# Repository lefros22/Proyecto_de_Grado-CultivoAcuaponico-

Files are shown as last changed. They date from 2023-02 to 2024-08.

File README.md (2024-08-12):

# Degree_Project-AquaponicCrop

In this repository you will find the documentation of "Design and implementation of an automation and control system for aquaponic crops in urban areas".

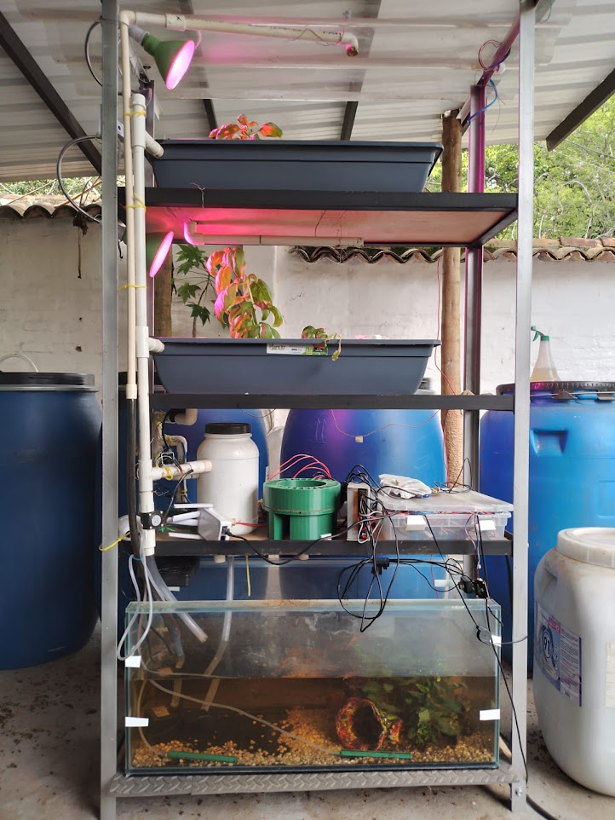
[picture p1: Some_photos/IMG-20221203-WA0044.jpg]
My Image


The main document is written in Spanish, but the documentation in this repository is in English.

Authors: 
- Luis Fernando Riveros Orozco
- Karen Yissel Marin Franco

Director:
- Juan Manuel Nogales

## Project summary
The project is the assembly of an aquaponic crop and the implementation of an automation system using hybrid predictive control with fuzzy to control the active elements of the crop.

The entire project is divided into the following components:
- Physical structure
- Web page
- IoT
- Control
- Management system

### Resume: 

This work presents an automation and control system for aquaponic crops in urban environments by employing a modern multivariable control technique. The prototype reached a level 7 on the Technology Readiness Level (TRL) scale and consists of an aquaponic crop in which water luminosity and temperature are controlled through a hybrid predictive control with fuzzy logic applied to four fundamental control variables: water oxygenation, circulation and aeration, and plant luminosity.

To operate the automation system, a webpage was built to provide access to remote control, supervision, and monitoring functionalities, as well as a management system based on Linux services and communicates via MQTT. The automation system uses a local network that allows communication between different system components (sensors, actuators, microprocessor, and microcontroller) and is capable of detecting internet connectivity status and taking actions in case of failure. Furthermore, the prototype demonstrates complete autonomy for a period of 3-5 days, attributed to the incorporation of a feeding dispenser. Moreover, the prototype also exhibits a semi-autonomous functionality of up to 20 days, achieved by regular replenishment of the dispenser every 4 days and maintenance of the filters by cleaning every 6 days

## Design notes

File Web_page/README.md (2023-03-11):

# Web Page

Technical description of the website:

- Server: hosted in firebase under the backendless paradigm.
- Technology: Node.js with the react framework.
- Database: firebase real-time.
- Architecture: By components, reusable views, OOP.

Here you can see:
- Desing process of the page
- Source code of the page
- Final views of the page

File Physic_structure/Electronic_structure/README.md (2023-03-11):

# Electronic_structure

In this folder you can see:

- ESP32_code: final code used in the proyect
- Dosage: Files of fedders
- Sensors_Detail: The detail of the sensor used in the project

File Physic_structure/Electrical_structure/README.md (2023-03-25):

# Electrical structure
Here you can see the used cable list

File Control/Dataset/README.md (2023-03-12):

# Dataset
Here you can see the excel files with the data used or generated in the notebooks

I consider it important to talk about "estimulos.xlsx" since it contains the combinations of the cycles applied in the data collection stage.

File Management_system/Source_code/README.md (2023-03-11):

# Management system

This folder contains the source code of the management system and the services files

## Folders: 

- **servicios:** the source code of program

- **services systemd:** the configuration archives to sytemd

- **service crontab:** the linux command for services in crontab

## Explanation of each of solution

### services executed with crontab
- Webcam: takes twenty photos, one photo every three seconds, and stores it in ram (Managed by crontab, runs it every minute).
- AskInternet: pings google and if successful, stores in ram(statusInternet) the value 'ON' that represents internet connectivity.

### python services executed with systemd
#### BD reading:
- **EstadoControl_service:** it is a listener of the control state in which the DB is found in the location "Control/stateControl" corresponding to the state of the control (Manual, Automatic, Emergency) and writes it to a ram file located in "Ram_Var/estado.txt”.
- **EstadoActuadores_service:** it is a listener of the actuators state that is found in "Control/Actuators" and when a change occurs, it writes it to a ram file "Ram_Var/actuadores.txt".
#### DB writing:
- **ActPinesBD_service:** subscribes to the "main/actuadores" topic, manages a JSON that contains the status that each actuator must have and when it receives a message, it updates (set) the status that was sent to it in the DB in the "Control/Actuadores" location .
- **SensoresBD_service:** It subscribes to the “esp32/sensor” topic, it manages a JSON that contains the measurement of the esp32 sensors and when it receives a message, it adds (push) the status that was sent to it in BD in the “DatosSensoresInterno” location.
- **MensajesBD_service:** is subscribed to the topic “main/mensajes” and when it receives a message, it sends it (push) to BD in the location “Mensajes”.
- **SensoresExtBD:** is subscribed to the topic “Main/sensorExr/#“ and when it receives a measurement result, it sends it (push) to BD in the location “DatosSensoresExterno”.
- **PredictionsBD_service:** is subscribed to the “PredictionsBD” topic and when it receives a result from the work cycles, it sends (push) them to BD in the “ControlPredictivoResult” location.
#### Publishers in mqtt
- **Desague_service:** reads the status of a GPIO port of the raspberry (drain sensor found in the drainage module of the physical assembly) and publishes an emergency message in the "main/messages" topic if activated.
- **LightSensor_service:** reads the result of an I2C luminosity sensor every minute and publishes the average of the measurement every two hours in the topic “Main/sensorExr/Ligth”.
- **ControlModerno:** it is a service of the execution type with a timer which is executed automatically every two hours and makes the prediction of the best combination of stimuli for the next interval, which writes in Ram ("Ram_Var/ciclos_pred.txt") and sends a message to the topic “PredictionsBD”.

#### Main
- **MainControl:** is the main service that reads variables stored in RAM and publishes to MQTT using commands with the subsystem library. It manages the ignition of the actuators depending on the time of day and also manages the measurement and dosage of feed. This service implements two threads, one for water circulation and the other for sensing. Additionally, depending on the internet connectivity, it activates the ON/OFF control as an emergency system, since the predictive needs information from the internet.
#### Others
- **PinesActuators:** it subscribes to the "main/actuatuadores" topic, it manages a JSON that contains the status that each actuator must have and when it receives a message, it updates the status that was sent to it in the GPIO ports.

### Python scripts:
- **Control_module:** contains two functions
  - *Porcentajes:* returns what status the different actuators should have depending on the time of day according to a predefined Json file.
  - *get_Porcentajes_predictivo:* returns the working percentages for the actuators according to the current state of the predictive control.

- **PictureBD:** Reads an image from the BD every three seconds, converts it to base64, and sends it to the BD.

- **RN:** script that loads the models (ML model, scaler dimensional model, standard scaler) and contains a function that executes the prediction by going through the three models.
- **FUZZY:** script that generates the value that should be applied according to the previous luminosity average.

### Files:
#### Models:
- **RNmodel:** model corresponding to the neural network (sklearn MLPregressor).
- **dim_scaler:** dimensional reduction model (sklearn PCA decomposition).
- **std_scaler:** normalization model (sklearn StandardScaler).

#### Variables in ram:
- **actuadores:** JSON file with the status of each actuator in the database.
- **status:** control status value (manual, automatic, emergency) found in the database.
- **last1Lum_sensor:** The last average luminosity measured.
- **last6_sensor:** JSON file with the record of the last 6 values measured in the fish tank.
- **ciclos_pred:** JSON file corresponding to the work percentages calculated by the predictive control.
- **Captura.jpg:** image corresponding to the photo captured by the camera
- **statusInternet:** value corresponding to the internet status

## ADDITIONAL
### Libraries used in this project

#### For Raspberry:

- **Mosquitto-broker:** used to set the raspberry pi as a bróker mqtt 
  - https://randomnerdtutorials.com/how-to-install-mosquitto-broker-on-raspberry-pi/

- **Mosquitto-client:** used to set the raspberry pi as a client mqtt
  - https://randomnerdtutorials.com/testing-mosquitto-broker-and-client-on-raspbbery-pi/

- **fswebcam:** used to take photos from usb camera in webcam.sh

#### For python:

- **paho.mqtt.client:** used for suscribe and create a client in python script
- **pyrebase:** used for make the conection to bd firebase-realtime
  - https://github.com/thisbejim/Pyrebase
- **DateTime:** used to get the current time and convert between date formats
- **rpi.gpio:** used to control the gpios of the raspberry and control the elements of action.
  - https://www.raspberrypi-spy.co.uk/2012/05/install-rpi-gpio-python-library/
- **smbus2:** used to read the measurement of the brightness sensor BH1750
  - [https://www.pololu.com/docs/0J73/15.9](https://www.pololu.com/docs/0J73/15.9)

### How to mount a space in ram
Replace "full_path" with the exact path where you want the ram folder, not including the "[]", also you can change the size in size, actual size is 30mb in the command
#### `sudo mount -t tmpfs -o rw,size=30m tmpfs [full_path]`

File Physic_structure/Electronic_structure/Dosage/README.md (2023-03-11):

# Dosage
STL files of the 2 versions of the feder together with an assembly 3d diagram

- Feeder Version 1: Feeder by storage hopper and endless screw driven by nema 17.
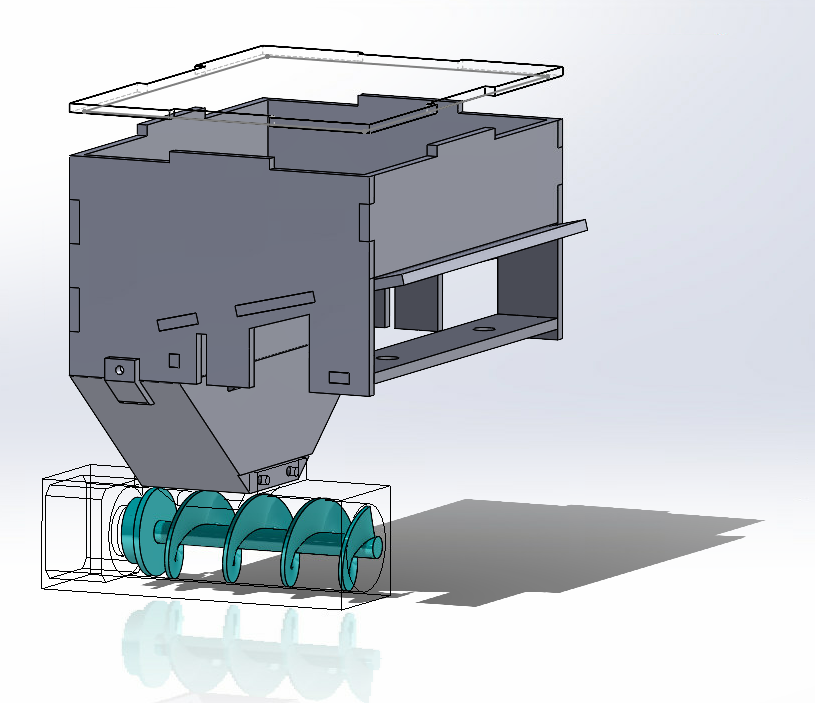
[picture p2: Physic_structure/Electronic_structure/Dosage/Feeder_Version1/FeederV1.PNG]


- Feeder Version 2: volumetric type doser by cell rotation powered by nema 17 and set of pulleys.
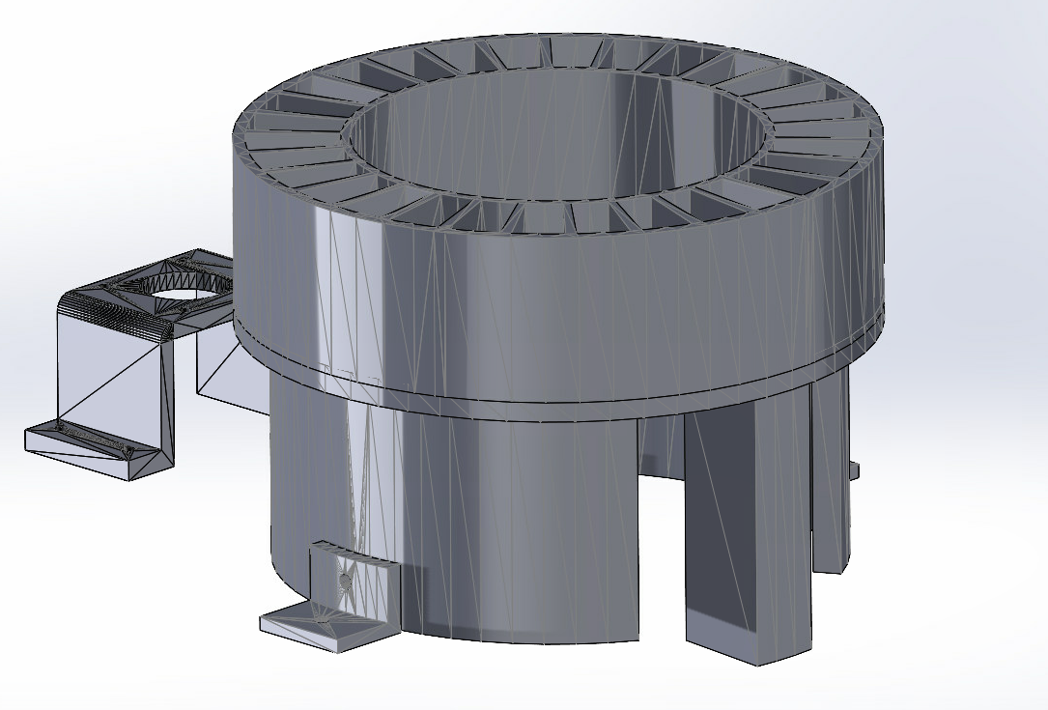
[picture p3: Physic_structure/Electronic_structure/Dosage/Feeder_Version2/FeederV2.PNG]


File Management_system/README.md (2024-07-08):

# Management system
This folder contains the documentation of the management system

The Management System it's implemented under services architecture using systemd and crontab in Linux with scripts in Python and Bash.

- Complete diagram of the architecture of services, modules and components

- Description of each script

- Script codes

- Service codes

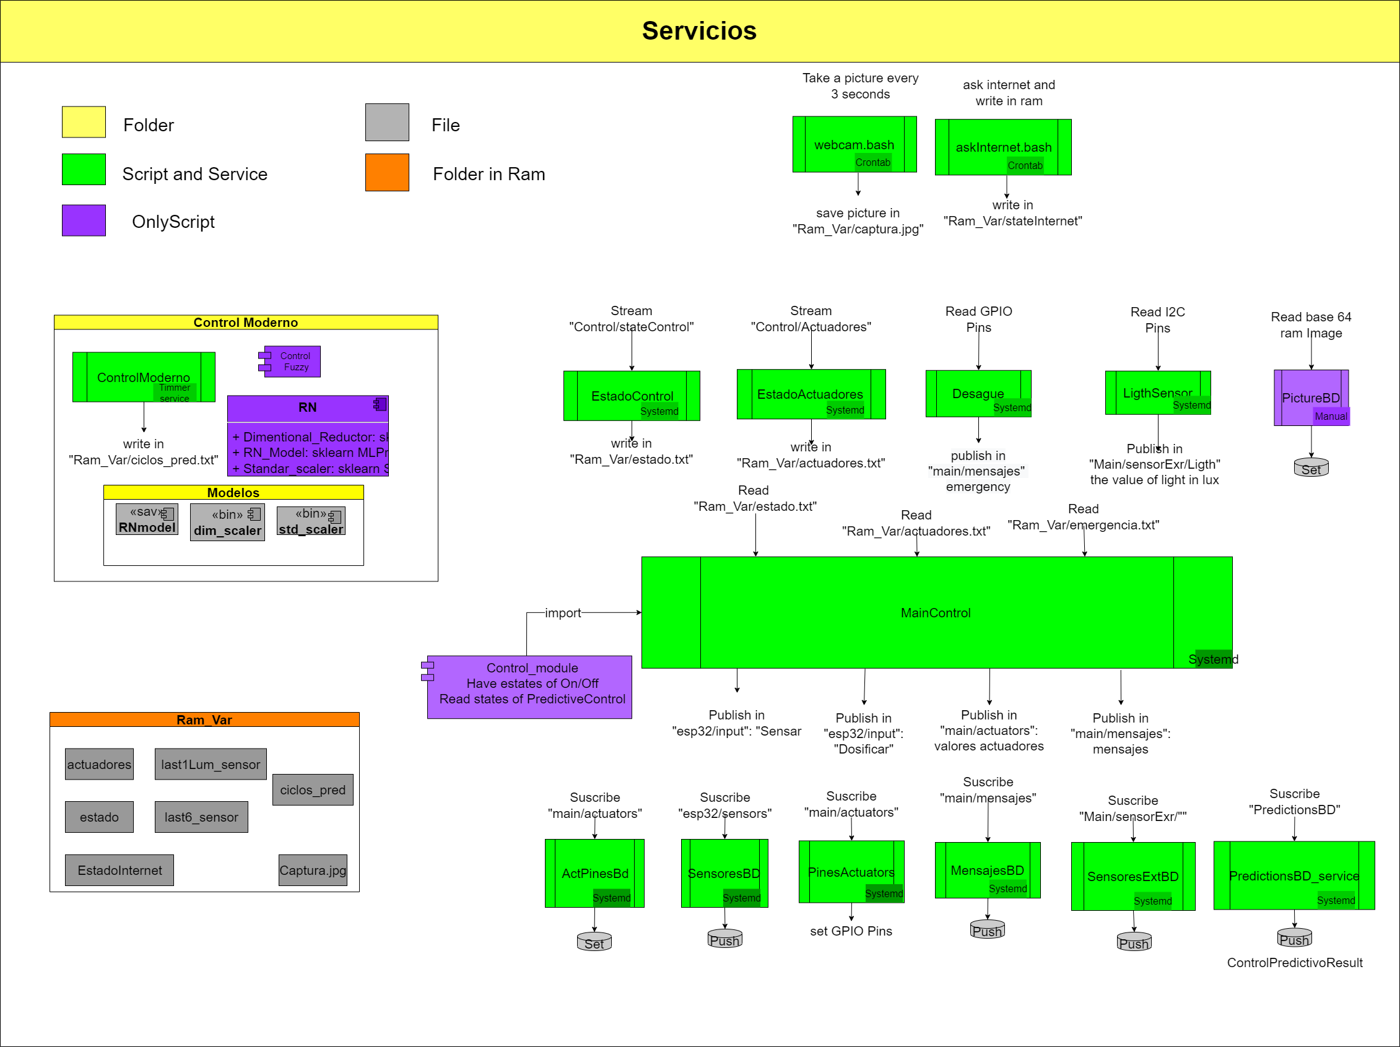
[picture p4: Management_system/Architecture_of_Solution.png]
My Image


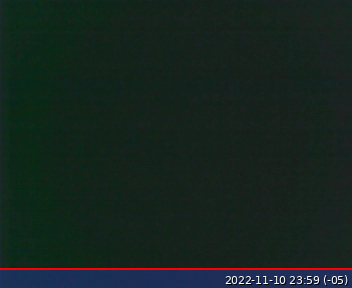
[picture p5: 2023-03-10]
Management_system/Source_code/Servicios/Ram_Var/captura.jpg

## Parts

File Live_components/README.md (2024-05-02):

# Live componets
Live components of the project are:

- Fishes
- Plants
- Bacteria

The photos in the nex link:

https://photos.app.goo.gl/17TKQxqVfbyk1X739

For description you can check the grade project document

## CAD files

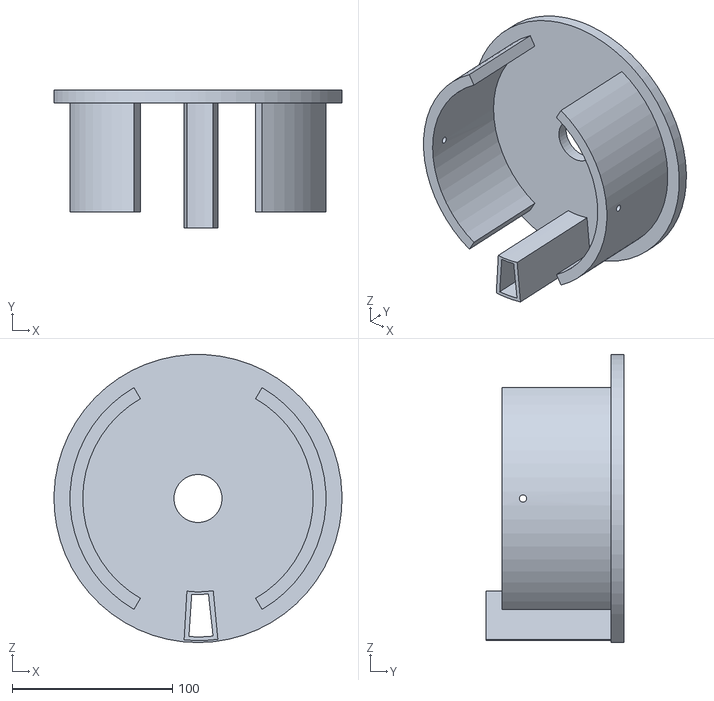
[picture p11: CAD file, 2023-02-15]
Physic_structure/Electronic_structure/Dosage/Feeder_Version2/pieza3.STL
179.9 x 86.0 x 180.0

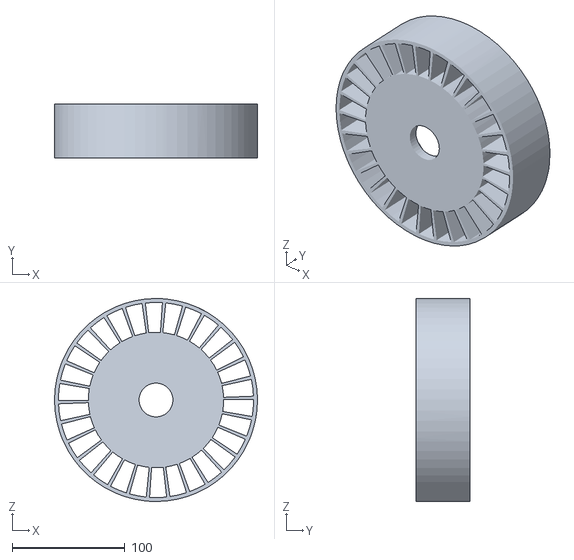
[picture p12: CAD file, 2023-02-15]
Physic_structure/Electronic_structure/Dosage/Feeder_Version2/pieza1.STL
180.0 x 48.0 x 180.0

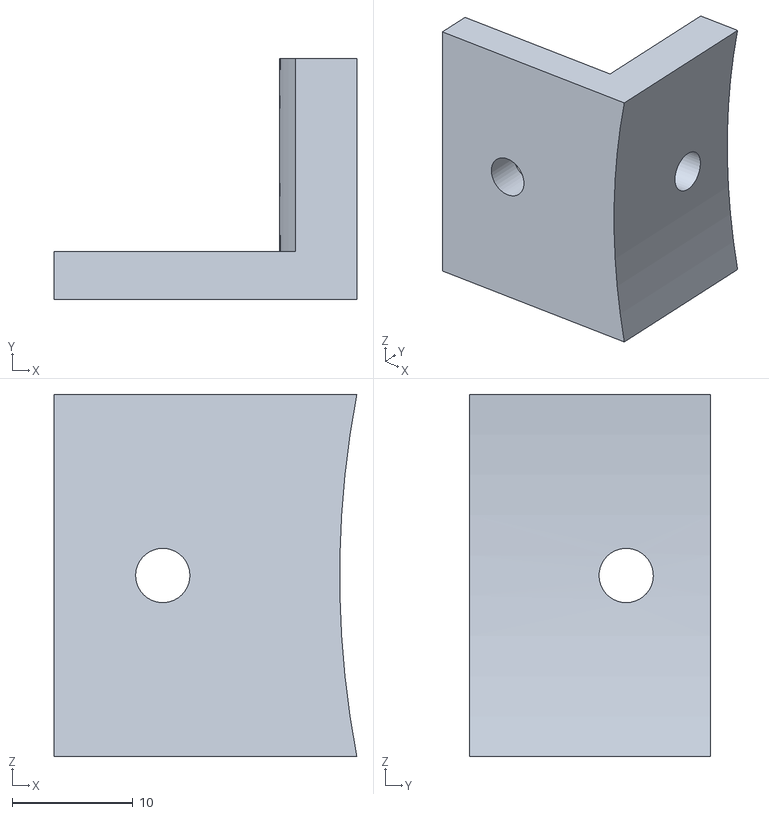
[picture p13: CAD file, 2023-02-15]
Physic_structure/Electronic_structure/Dosage/Feeder_Version2/pieza4x2.STL
25.1 x 20.0 x 30.0

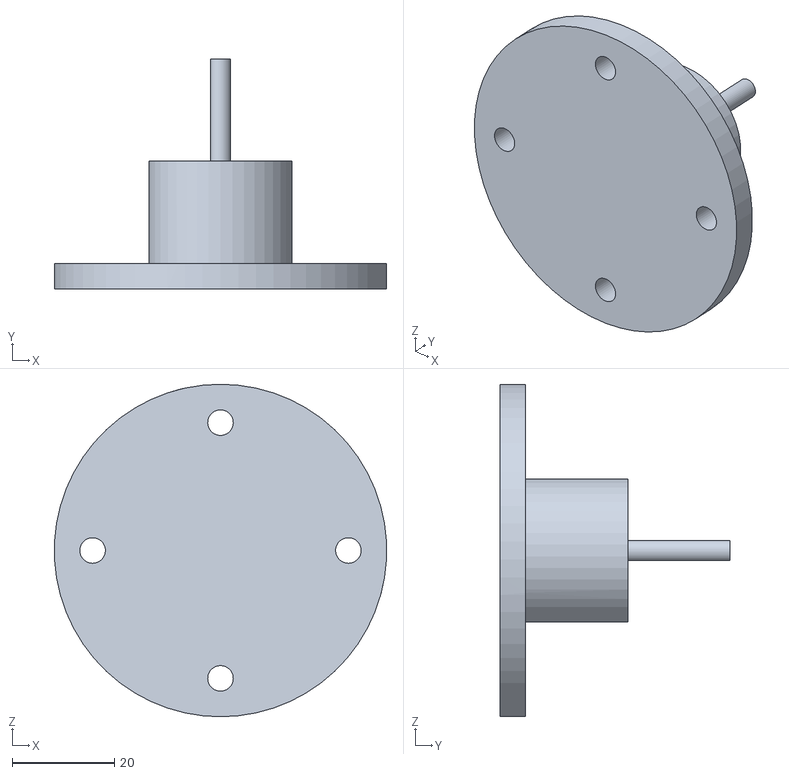
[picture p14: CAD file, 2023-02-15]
Physic_structure/Electronic_structure/Dosage/Feeder_Version2/pieza2.STL
64.9 x 45.0 x 65.0

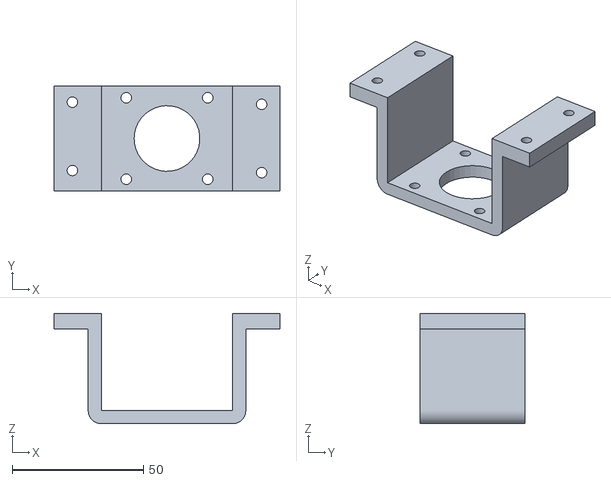
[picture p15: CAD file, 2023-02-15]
Physic_structure/Electronic_structure/Dosage/Feeder_Version2/pieza5.STL
86.0 x 40.0 x 42.0

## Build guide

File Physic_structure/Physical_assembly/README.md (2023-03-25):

# Physic structure

Here you can see the used pipe materials

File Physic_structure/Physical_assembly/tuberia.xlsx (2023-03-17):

Imagen | Nombre | Cantidad
 | Tubo presión 1/2-pulg x 6mts 9-500 PSI | 1
 | Unión hembra roscada 1/2 Presión | 16
 | Codo 90 x 1/2 presión | 24
 | Tee 1/2 presión | 8
 | Unión 1/2 presión | 8
 | Tapon Roscado Presión 1/2 | 2
 | Adaptador Macho Presión 1/2 | 2

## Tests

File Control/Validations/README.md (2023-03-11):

# RN

- **Correlation Matrix Notebook:** Here you can see an example of the notebook used to evaluate the correlation in a time interval, only that it can be subject to bias due to the complexity in the interactions of the system, it is more a reference measure than an accurate validation.
- **Control validation Excel:** To analyze how consistently the network responded based on different data and conditions, 30 random samples were extracted from the dataset and the percentages of cycles were iterated in the 16 possible peak combinations (0%, 100%) in each of the actuators.
The results were consistent for all 30 samples. In this file you can see a summary table with the calculations made for 10 neural networks.

  - In sheet Combination strategy you can find the 16 combinations of maximum and minimum used in the analysis
  - In sheet Analysis you can find the nex tables:
    - ***Comparison with respect to not exercising actions:*** In this table you can see the variation of each of the action sets with respect to set 0 (do nothing, review the previous page).From here, the maximum possible real variation is obtained, which is the subtraction between the maximum positive variation vs. the maximum negative variation, with which the real variation is obtained.
    - ***Mean step response for each variable:*** Here is summarized the variation of the previous table for the unit step responses of each of the action variables while the rest are set to 0. In addition, it is calculated how representative this change is in contrast to the maximum possible variation between cases of the previous table
    - ***Sign consistency in changes:*** Here the consistency of the variations is analyzed, seen in another way, if the variations are an accidental or real fact that the network manages to interpret, the results indicated that for TDS 10/10 networks generate the same sign of variation (positive or negative). in each of the 16 cases, while for Temperature 97% of the cases are consistent.

## Conclusion
According to the previous results, it is validated that the system is controllable to some extent indirectly.

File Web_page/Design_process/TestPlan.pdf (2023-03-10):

Propuesta de plan de pruebas

Teniendo en cuenta la etapa en la que se encuentra el proyecto. Aún no se puede comprobar la funcionalidad en la vida real (pues aún no está montado el cultivo) y además las interacciones con el usuario no están implementadas por completo.

Lo que sí podemos evaluar, son las funcionalidades principales que ya se encuentran dentro de la aplicación web y la dinámica de usuario al momento de usar la app.

Se decidió hacer una entrevista vía zoom en donde el usuario en un primer momento se le da una contextualización del proyecto, posteriormente se le deja controlar la pantalla para usar la app web y por último se le da una encuesta al final de la sesión.

La encuesta se divide en 4 partes:

-Interfaz: en la cual se evalúan los colores y la tipografía.

-Funcionalidades de monitoreo: en la cual se pregunta si las funcionalidades que posee la página son claras, pues las interacciones no están completamente implementadas y la parte gráfica tampoco está hecha por completo.

-Funcionalidades de control: una sección en donde se evalúa estándar y claridad para un usuario conocedor del tema(pues no está pensado para cualquier persona) sin embargo si se deja espacio de opiniones para otro tipo de usuario(que solo necesitan ver).

-Por último, un espacio para sugerencias adicionales que no están en ninguna de las categorías.

Link de la encuesta: https://forms.office.com/r/QxUnHLuaG0

Evaluación heurística de la aplicación por parte de grupo par

Grupo evaluador: Ghina Garces, Jesus Valencia, Stefania Hurtado.

Problema: Accesibilidad de las variables de
monitoreo

Severidad: 2

Heurística violada: 8. Estética y diseño minimalista

Descripción: Los rolldown menús que usar actualmente para acceder a las variables monitoreadas son difíciles de usar y requieren muchos clicks en comparación a otras formas de separación de contenido como las pestañas que, además, son más apegadas al estándar al que la gente está acostumbrada.

Problema: Visualización del tiempo

Severidad: 2

Heurística violada: 4. Consistencia y estándares

Descripción: En vez de permitirle al usuario definir con un input la cantidad de tiempo que quiere visualizar, se puede usar rangos de tiempo estandarizados como: 24 horas, 1 semana, 1 mes, etc y quizás agregar una opción más personalizada pero darle así más facilidad al usuario al acceder a la información que le interesa.

Problema: Señalización de objetos clickeables Severidad: 2 Heurística violada: 6. Reconocer en lugar de recordar Descripción: Si bien el software está hecho para personas con conocimiento en el tema, muchas veces es más fácil reconocer qué y dónde se hace cada cosa si hay alguna pista visual en vez de tener que recordar de memoria que significa cada cosa. Esto también ayuda a usuarios nuevos, en procesos de capacitación o que apenas están acostumbrándose al software. | Problema: Contraste entre fondos y fuentes Severidad: 1 Heurística violada: ninguna Descripción: Algunas secciones tienen una diferencia de color entre el color de fondo y el color de la fuente demasiado baja para lo que es recomendado. Esto no solo hace más difícil de leer el texto sino que puede ser completamente ilegible según la configuración de otras pantallas.

Problema: Diseño anticuado Severidad: 1 Heurística violada: ninguna Descripción: El diseño estético no se apega a los estándares de diseño, lo que hace que se vea un poco cargado a pesar de ser muy simple. Esto carga la vista

Desarrollo de la evaluación

Debido a que mi trabajo está centrado en mi proyecto de grado, se decidió por usuarios en diversos casos.

- El primero es mi compañera de trabajo de grado(persona muy enterada del tema)
Karen Marin
- El segundo es una compañera de mi carrera(alguien que sabe de control y monitoreo más no de cultivos)
Daniela Melendez
- El tercero es una egresada de administración de empresas(alguien que conoce de supervisión y aspectos relacionados a software de oficina )
Carolina Gutiérrez
- El cuarto es una estudiante de Derecho(persona completamente ajena a este tipo de software o cuerpo de conocimiento pero que posee una formación académica) Natalia Palacios

Resultados Para la interfaz: Los usuarios están satisfechos un 4/5 en promedio con los colores utilizados. Los usuarios están satisfechos un 4.75/5 en promedio con la letra utilizada. Para la sección de monitoreo: A todos los usuarios les parece claro Para la sección de control: Para los usuarios que aplican, les parece acorde a los estándares y claro. Comentarios adicionales:

Interfaz | Monitoreo | Control | Adicionales
●Que la página
muestre en qué
casilla está ubicada; el
color azul de la barra
de arriba un poco
más claro
●En cuanto al diseño
agregarle recuadros a
cada sección para
hacerlo más
interactivo y
agradable a la vista
●El color del logo en
la parte superior no
es del mismo color
que las letras, se ve
mal eso
●Algunos colores
como el azul agua
marina no me parece
agradable a la vista

●Que la gráfica de
monitoreo sea un
poco más grande
●Agregar gráficos
interactivos que
permitan evaluar de
mejor manera las
variables ●Que
muestre en cuál
pestaña está

●Organizar los datos
(fecha y hora) de
forma diferente, de
manera que sea más
ameno visualmente
●Sería bueno añadir
cuadro de
información de los
conceptos
presentados

●La interfaz podría
tener una sesión para
el jefe del área que le
permita visualizar
todos/Varios tipos de
cultivo (por tema de
control) , y otra para
cada responsable o
usuario de un cultivo
específico ●Explicar
qué significan los
círculos que se ven
abajo de la imagen
cuando se está en la
pestaña de control
●La letra en la parte
de control, podría
diferenciarla
dividendo en
columnas, aumentar
la letra o aplicando
negrilla

Conclusiones

- En primer lugar, se logra evidenciar que los usuarios manifiestan algunas de las heurísticas violadas.
- En segundo lugar, se logran apreciar algunas perspectivas que no se habían tenido en cuenta
- Algunas funcionalidades adicionales solicitadas por los usuarios son extremadamente importantes y aun asi no se habían tenido en cuenta al inicio(como lo es un simbolo de mas informacion al lado de cada mensaje)
- Hacer un zoom con el usuario fue extremadamente importante, pues ayudó en el proceso de interpretar sus sugerencias, pues son escritas de la manera en que ellos entienden las cosas, pero al estar con ellos, se presenta la posibilidad de que expliquen sus sugerencias y así se pueda obtener una realimentación más acorde a lo que quieren expresar.
- La evaluación de heurísticas realizada por el otro grupo, me ha parecido pertinente y la tendré en cuenta para refinar la app.

Anexo Resultados completos de la encuesta:

https://docs.google.com/spreadsheets/d/1xbltt4YSdvfoay8ka8-Hjm756C9ov-gQ/edit?oui#gid=1673889053 (https://docs.google.com/spreadsheets/d/1xbltt4YSdvfoay8ka8-Hjm756C9ov-gQ/edit?oui#gid=1673889053)

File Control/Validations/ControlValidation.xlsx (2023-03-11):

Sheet: Combination strategy
Action elements
 | LUMINOSIDAD | CIRCULACION | OXIGENACION | AIREACION | Step combination
0 | 0 | 0 | 0 | 0
1 | 0 | 0 | 0 | 1 | A
2 | 0 | 0 | 1 | 0 | O
3 | 0 | 0 | 1 | 1
4 | 0 | 1 | 0 | 0 | C
5 | 0 | 1 | 0 | 1
6 | 0 | 1 | 1 | 0
7 | 0 | 1 | 1 | 1
8 | 1 | 0 | 0 | 0 | L
9 | 1 | 0 | 0 | 1
10 | 1 | 0 | 1 | 0
11 | 1 | 0 | 1 | 1
12 | 1 | 1 | 0 | 0
13 | 1 | 1 | 0 | 1
14 | 1 | 1 | 1 | 0
15 | 1 | 1 | 1 | 1

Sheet: Analysis
 | ANN'S
 | 1 |  | 2 |  | 3 |  | 4 |  | 5 |  | 6 |  | 7 |  | 8 |  | 9 |  | 10
 | TDS | TEMP | TDS | TEMP | TDS | TEMP | TDS | TEMP | TDS | TEMP | TDS | TEMP | TDS | TEMP | TDS | TEMP | TDS | TEMP | TDS | TEMP
0 | 193.8331388 | 23.04227675 | 193.8366538 | 23.02874223 | 193.8347151 | 23.04853602 | 193.8360681 | 23.03848886 | 193.8354222 | 23.04090057 | 193.8349778 | 23.0364926 | 193.8352058 | 23.05261975 | 193.8343985 | 23.04062805 | 193.8349672 | 23.04147183 | 193.8354952 | 23.03683995
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

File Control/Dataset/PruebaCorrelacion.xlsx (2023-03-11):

Fecha | Lum_n1 | Lum_n2 | Lum_n3 | Lum_n4 | Lum_n5 | Lum_n6 | TDS_n1 | TDS_n2 | TDS_n3 | TDS_n4 | TDS_n5 | TDS_n6 | Temp_n1 | Temp_n2 | Temp_n3 | Temp_n4 | Temp_n5 | Temp_n6 | Hora | CL | CC | CO | CA | TDS | Temp
01/10/2023, 12:03:21 | nan | nan | nan | nan | nan | nan | 389.7452087 | 392.5926514 | 389.7452087 | 387.819397 | 393.750946 | 391.389679 | 20.0 | 19.875 | 20.0 | 20.0625 | 20.125 | 20.5 | 10.0 | 0.45 | 0.98 | 0.39 | 0.96 | 392.8748169 | 20.75
01/10/2023, 14:03:21 | nan | nan | nan | nan | nan | nan | 392.8748169 | 389.7452087 | 392.5926514 | 389.7452087 | 387.819397 | 393.750946 | 20.75 | 20.0 | 19.875 | 20.0 | 20.0625 | 20.125 | 12.0 | 0.003333333333333333 | 0.96 | 0.34 | 0.97 | 393.2601318 | 21.6875
01/10/2023, 16:03:21 | nan | nan | nan | nan | nan | nan | 393.2601318 | 392.8748169 | 389.7452087 | 392.5926514 | 389.7452087 | 387.819397 | 21.6875 | 20.75 | 20.0 | 19.875 | 20.0 | 20.0625 | 14.0 | 0.003333333333333333 | 0.96 | 0.49 | 0.97 | 393.9291992 | 21.875
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

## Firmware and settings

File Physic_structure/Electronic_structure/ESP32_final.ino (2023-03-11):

/*********
  Luis Riveros
  Complete project details at https://github.com/lefros22/Proyecto_de_Grado-CultivoAcuaponico-
*********/
//Lybrary comunication
#include <WiFi.h>
#include <PubSubClient.h>
#include <Wire.h>
//Librarys SENSORS AND OTHER
#include <HardwareSerial.h>
#include <Arduino.h>
#include <ArduinoJson.h>
#include <OneWire.h>
#include <DallasTemperature.h>

// Replace the next variables with your SSID/Password combination
//const char* ssid = "LUIS1234";
//const char* password = "luisloco";
const char* ssid = "LuisyKaren";
const char* password = "luismanda";


// Add your MQTT Broker IP address, example:
//const char* mqtt_server = "192.168.1.144";
//const char* mqtt_server = "192.168.134.57";
const char* mqtt_server = "192.168.7.4";
WiFiClient espClient;
PubSubClient client(espClient);
const char* device_name="ESP32";
long lastMsg = 0;
char msg[50];
int value = 0;

//uncomment the following lines if you're using SPI
/*#include <SPI.h>
#define BME_SCK 18
#define BME_MISO 19
#define BME_MOSI 23
#define BME_CS 5*/



//GLOBALS GENERIC
#define VREF 3.3     
StaticJsonDocument<500> VarSensadas;
char result[500];

//----VARIABLES SENSORES-----
//------Turbidez-------
#define TurbidezSensorPin 32
#define TURBIDEZ_Samples  30            // sum of sample point

int TURBIDEZ_analogBuffer[TURBIDEZ_Samples];     // store the analog value in the array, read from ADC
int TURBIDEZ_Index = 0;
float TURBIDEZ_averageVoltage = 0;
float turbidezValue = 0;
//--------Temperature-----
// GPIO where the DS18B20 is connected to
const int oneWireBus = 4;     
float temperature = 25;       // current temperature for compensation
// Setup a oneWire instance to communicate with any OneWire devices
OneWire oneWire(oneWireBus);
// Pass our oneWire reference to Dallas Temperature sensor 
DallasTemperature sensors(&oneWire);
//--------TDS-------
#define TdsSensorPin 33
#define TDS_Samples  30            // sum of sample point

int TDS_analogBuffer[TDS_Samples];     // store the analog value in the array, read from ADC
int TDS_Index = 0;
float TDS_averageVoltage = 0;
float tdsValue = 0;
//-----PH------
#define PHSensorPin 34            //pH meter Analog output to Arduino Analog Input 0
#define ph_Offset 0.10            //deviation compensate
#define PH_Samples  30

int PH_analogBuffer[PH_Samples];     // store the analog value in the array, read from ADC
int PH_Index = 0;
float PH_averageVoltage = 0;
float phValue = 0;

//------OD------
#define ODSensorPin 35            //pH meter Analog output to Arduino Analog Input 0
#define OD_Samples  30
#define VREF2 3300    //VREF (mv)
#define ADC_RES 4096 
uint16_t ADC_Raw;
uint16_t ADC_Voltage;
uint16_t odValue;


//Single point calibration needs to be filled CAL1_V and CAL1_T
#define CAL1_V (1050) //mv
#define CAL1_T (25)   //℃
//Two-point calibration needs to be filled CAL2_V and CAL2_T
//CAL1 High temperature point, CAL2 Low temperature point
#define CAL2_V (1300) //mv
#define CAL2_T (15)   //℃

const uint16_t DO_Table[41] = {
    14460, 14220, 13820, 13440, 13090, 12740, 12420, 12110, 11810, 11530,
    11260, 11010, 10770, 10530, 10300, 10080, 9860, 9660, 9460, 9270,
    9080, 8900, 8730, 8570, 8410, 8250, 8110, 7960, 7820, 7690,
    7560, 7430, 7300, 7180, 7070, 6950, 6840, 6730, 6630, 6530, 6410};

int16_t readDO(uint32_t voltage_mv, uint8_t temperature_c)
{
  uint16_t V_saturation = (uint32_t)CAL1_V + (uint32_t)35 * temperature_c - (uint32_t)CAL1_T * 35;
  return (voltage_mv * DO_Table[temperature_c] / V_saturation);
}
//----END VARIABLES SENSORES-----

//-----FEDDER VARIABLES-----
#define EN_PIN    13 //enable (CFG6)
#define STEP_PIN  12 //step
#define DIR_PIN   27 //direction
int cant_pasos_fedder=96;
int fedder_Index=0;

//-----END FEDDER VARIABLES-----

// ------------SENSORS ------------
void Sense_temperature(){
  sensors.requestTemperatures(); 
  temperature= sensors.getTempCByIndex(0);
  VarSensadas["TEMP"]=temperature;
  }
// ------------Turbity---------------
void Sense_turbidez(){
  for(TURBIDEZ_Index=0; TURBIDEZ_Index<TURBIDEZ_Samples; TURBIDEZ_Index++){
    TURBIDEZ_analogBuffer[TURBIDEZ_Index] = analogRead(TurbidezSensorPin);    //read the analog value and store into the buffer
    delay(5);
    //wait 40ms
  }
  // read the analog value more stable by the median filtering algorithm, and convert to voltage value
  TURBIDEZ_averageVoltage = (getMedianNum(TURBIDEZ_analogBuffer,TURBIDEZ_Samples) * (float)VREF / 4096.0)-1.5;
  //convert voltage value to tds value
  turbidezValue=1.0/(TURBIDEZ_averageVoltage*10+0.0001);
  VarSensadas["TURBIDEZ"]=turbidezValue;
}


// ------------TDS---------------

void Sense_TDS(){
  for(TDS_Index=0; TDS_Index<TDS_Samples; TDS_Index++){
    TDS_analogBuffer[TDS_Index] = analogRead(TdsSensorPin);    //read the analog value and store into the buffer
    delay(5);
    //wait 40ms
  }
  // read the analog value more stable by the median filtering algorithm, and convert to voltage value
  TDS_averageVoltage = getMedianNum(TDS_analogBuffer,TDS_Samples) * (float)VREF / 4096.0;
  //temperature compensation formula: fFinalResult(25^C) = fFinalResult(current)/(1.0+0.02*(fTP-25.0)); 
  float compensationCoefficient = 1.0+0.02*(temperature-25.0);
  //temperature compensation
  float compensationVoltage=TDS_averageVoltage/compensationCoefficient;
  //convert voltage value to tds value
  tdsValue=(133.42*compensationVoltage*compensationVoltage*compensationVoltage - 255.86*compensationVoltage*compensationVoltage + 857.39*compensationVoltage)*0.5;
  VarSensadas["TDS"]=tdsValue;
  //send msj queque tdsValue;
}
// ------------PH------------
void Sense_PH(){
  for(PH_Index=0; PH_Index<PH_Samples; PH_Index++){
    PH_analogBuffer[PH_Index] = analogRead(PHSensorPin);    //read the analog value and store into the buffer
    delay(5);
    //wait 40ms
  }
  // read the analog value more stable by the median filtering algorithm, and convert to voltage value
  PH_averageVoltage = getMedianNum(PH_analogBuffer,PH_Samples) * (float)VREF / 4096.0;
  //convert voltage value to ph value
  phValue = 6.2*PH_averageVoltage+ph_Offset;
  VarSensadas["PH"]=phValue;
  Serial.println(PH_averageVoltage);
  //send msj queque tdsValue;
}
// ------------OD------------
void Sense_OD(){
  ADC_Raw = analogRead(ODSensorPin);
  ADC_Voltage = uint32_t(VREF2) * ADC_Raw / ADC_RES;
  //send msj queque tdsValue;
  odValue = readDO(ADC_Voltage, uint16_t(temperature));
  VarSensadas["OD"]= String(odValue);
}

// ------------FEDDER------------
void Dosificar_Fedder(){
  for(fedder_Index=0; fedder_Index<cant_pasos_fedder; fedder_Index++){
  //make steps
    digitalWrite(STEP_PIN, HIGH);
    delay(5);
    digitalWrite(STEP_PIN, LOW);
    delay(5); 

  }
}
// ------------END SENSORS------------

// median filtering algorithm
int getMedianNum(int bArray[], int iFilterLen){
  int bTab[iFilterLen];
  for (byte i = 0; i<iFilterLen; i++)
  bTab[i] = bArray[i];
  int i, j, bTemp;
  for (j = 0; j < iFilterLen - 1; j++) {
    for (i = 0; i < iFilterLen - j - 1; i++) {
      if (bTab[i] > bTab[i + 1]) {
        bTemp = bTab[i];
        bTab[i] = bTab[i + 1];
        bTab[i + 1] = bTemp;
      }
    }
  }
  if ((iFilterLen & 1) > 0){
    bTemp = bTab[(iFilterLen - 1) / 2];
  }
  else {
    bTemp = (bTab[iFilterLen / 2] + bTab[iFilterLen / 2 - 1]) / 2;
  }
  return bTemp;
}

// ------------------SETUP BEGIN----------
void setup() {
  //COMUNICAION MQTT
  Serial.begin(115200);
  // default settings
  // (you can also pass in a Wire library object like &Wire2)
  //status = bme.begin();  
  setup_wifi();
  client.setServer(mqtt_server, 1883);
  client.setCallback(callback);
  //SENSORS
    //tds sensor
  pinMode(TdsSensorPin,INPUT);
  pinMode(TurbidezSensorPin,INPUT);
  pinMode(PHSensorPin,INPUT);
  pinMode(oneWireBus, INPUT_PULLUP);
  // Start the DS18B20 sensor
  sensors.begin();

  //FEDDER
  //set pin modes
  pinMode(EN_PIN, OUTPUT);
  digitalWrite(EN_PIN, HIGH); //deactivate driver (LOW active)
  pinMode(DIR_PIN, OUTPUT);
  digitalWrite(DIR_PIN, LOW); //LOW or HIGH
  pinMode(STEP_PIN, OUTPUT);
  digitalWrite(EN_PIN, LOW); //activate driver

}

void setup_wifi() {
  delay(10);
  // We start by connecting to a WiFi network
  Serial.println();
  Serial.print("Connecting to ");
  Serial.println(ssid);

  WiFi.begin(ssid, password);

  while (WiFi.status() != WL_CONNECTED) {
    delay(500);
    Serial.print(".");
  }

  Serial.println("");
  Serial.println("WiFi connected");
  Serial.println("IP address: ");
  Serial.println(WiFi.localIP());
}

void callback(char* topic, byte* message, unsigned int length) {
  Serial.print("Message arrived on topic: ");
  Serial.print(topic);
  Serial.print(". Message: ");
  String messageTemp;
  
  for (int i = 0; i < length; i++) {
    messageTemp += (char)message[i];
  }
  Serial.println(messageTemp);

  // Feel free to add more if statements to control more GPIOs with MQTT

  // If a message is received on the topic esp32/output, you check if the message is either "on" or "off". 
  // Changes the output state according to the message
  if (String(topic) == "esp32/input") {
    client.publish("esp32/output", "Recibi un mensaje");
    if(messageTemp == "Sensar"){
      Sense_temperature();
      Sense_TDS();
      Sense_PH();
      Sense_turbidez();
      Sense_OD();
      serializeJson(VarSensadas,result);
      client.publish("esp32/sensors", result);
      Serial.println("result:");
      Serial.println(result);
    }
    else if(messageTemp == "Dosificar"){
      Dosificar_Fedder();
      client.publish("esp32/output", "Dosifico");
    }
    else{
      client.publish("esp32/output", "No clasificado");
      }
  }
}

void reconnect() {
  // Loop until we're reconnected
  while (!client.connected()) {
    Serial.print("Attempting MQTT connection...");
    // Attempt to connect
    if (client.connect(device_name)) {
      Serial.println("connected");
      // Subscribe
      client.publish("esp32/output", "holis2");
      client.subscribe("esp32/input");
    } else {
      Serial.print("failed, rc=");
      Serial.print(client.state());
      Serial.println(" try again in 5 seconds");
      // Wait 5 seconds before retrying
      delay(5000);
    }
  }
}
// ------------------END SETUP BEGIN----------

//-------------MAIN LOOP--------------------
void loop() {
  if (!client.connected()) {
    reconnect();
  }
  client.loop();
}
//-------------END MAIN LOOP--------------------

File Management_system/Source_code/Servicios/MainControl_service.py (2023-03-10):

#!/usr/bin/python3
from time import sleep
import json
import datetime as dt
import subprocess as sp
import os
import threading
#mod control
import Control_module

#messages
genericoOnOFF =  '{ "Tipo":"generico", "Descripcion":"control On/off funcionando"}'
genericoPredictivo =  '{ "Tipo":"generico", "Descripcion":"control Predictivo funcionando"}'

genericoNuevoCiclo =  '{ "Tipo":"generico", "Descripcion":"inicio Nuevo ciclo"}'

genericoDosificacion =  '{ "Tipo":"generico", "Descripcion":"se dosifica alimento"}'


#Funciones de ciclo
horas_ciclo = 2
#Devuelve la hora de 00 a 23
def obtener_hora():
    return dt.datetime.now().hour

# Devuelve los minutos de 00 a 59
def obtener_minutos():
    return dt.datetime.now().minute

def obtener_segundos():
    return dt.datetime.now().second
#Definir en qué ciclo del día está
def ciclo_dia():
    global horas_ciclo
    ciclo = (obtener_hora() // horas_ciclo) + 1
    return ciclo
def porcentaje_de_ciclo():
    suma_minutos = obtener_minutos() / 60
    hora_min = obtener_hora() + suma_minutos
    modulo = hora_min % horas_ciclo
    porcentaje_ciclo = modulo / horas_ciclo
    return porcentaje_ciclo



#Automatizacion general
Val_Actuadores ={"AirPump": True,"Fan": False,"Feeder": False,"Humidifer1": False,"Humidifer2": False,"Lamp1": False,"Lamp2": False,"Peristaltic1": False,"Peristaltic2": False,"Valve1": False,"Valve2": False,"ValveIn": False,"WaterPump1": False,"WaterPump2": False,"SensoresVcc": False}

Val_Actuadores_emergencia ={"AirPump": True,"Fan": False,"Feeder": False,"Humidifer1": False,"Humidifer2": False,"Lamp1": False,"Lamp2": False,"Peristaltic1": False,"Peristaltic2": False,"Valve1": False,"Valve2": False,"ValveIn": False,"WaterPump1": False,"WaterPump2": False,"SensoresVcc": False}


plantas_iluminadas = False
peces_alimentados = False
plantas_humectadas = False
agua_circulada = False
agua_oxigenada = False
agua_aireada = False


def activacion_acciones_porcentaje(porcentajes):
    porcentaje_actual = porcentaje_de_ciclo()+0.01
    #Iluminacion plantas
    iluminacion_plantas(porcentaje_actual,porcentajes["porc_iluminacion"])
    #Iluminacion plantas
    humectacion_plantas(porcentaje_actual,porcentajes["porc_humectacion"])
    #Circulacion agua
    circulacion_agua(porcentaje_actual,porcentajes["porc_circulacion"])
    #Oxigenacion agua
    oxigenacion_agua(porcentaje_actual,porcentajes["porc_oxigenacion"])
    #Aireacion agua
    aireacion_agua(porcentaje_actual,porcentajes["porc_aireacion"])


def iluminacion_plantas(pa,po):
    #print("funcion de iluminacion",)
    global Val_Actuadores,plantas_iluminadas
    if (pa<po):
        Val_Actuadores["Lamp1"] = True
        Val_Actuadores["Lamp2"] = True
    else:
        Val_Actuadores["Lamp1"] =False
        Val_Actuadores["Lamp2"] = False
        plantas_iluminadas = True

def humectacion_plantas(pa,po):
    #print("funcion de humectacion")
    global Val_Actuadores,plantas_humectadas
    if (pa<po):
        Val_Actuadores["Humidifer1"] = True
        Val_Actuadores["Humidifer2"] = True
    else:
        Val_Actuadores["Humidifer1"] =False
        Val_Actuadores["Humidifer2"] = False
        plantas_humectadas = True


def oxigenacion_agua(pa,po):
    #print("funcion de oxigenacion")
    global Val_Actuadores,agua_oxigenada
    if (pa<po): Val_Actuadores["AirPump"] = True
    else:
        Val_Actuadores["AirPump"] =False
        agua_oxigenada = True


def aireacion_agua(pa,po):
    #print("funcion de aireacion")
    global Val_Actuadores,agua_aireada
    if (pa<po): Val_Actuadores["Fan"] = True
    else:
        Val_Actuadores["Fan"] =False
        agua_aireada = True

def thread_circulacion():
    global Val_Actuadores
    Val_Actuadores["WaterPump1"] =True
    sleep(10)
    Val_Actuadores["WaterPump1"] =False
    sleep(150)
    
my_thread_circulacion = threading.Thread(target=thread_circulacion)
def circulacion_agua(pa,po):
    #print("funcion de aireacion")
    global Val_Actuadores,agua_aireada,my_thread_circulacion
    if (pa<po): 
        if not my_thread_circulacion.is_alive():
            my_thread_circulacion = None
            my_thread_circulacion = threading.Thread(target=thread_circulacion)
            my_thread_circulacion.start()
    else:
        Val_Actuadores["WaterPump1"] =False
        agua_aireada = True

def dosificar(ci):
    if ci in (5,7,8,9,10):
        os.system('mosquitto_pub -h localhost -t "esp32/input" -m "Dosificar"')
        os.system("mosquitto_pub -h localhost -t 'main/mensajes' -m '"+genericoDosificacion+"'")

def apagarsensor():
    global Val_Actuadores
    sleep(2)
    os.system('mosquitto_pub -h localhost -t "esp32/input" -m "Sensar"')
    sleep(50)
    Val_Actuadores["SensoresVcc"] =False

def sensar():
    Val_Actuadores["SensoresVcc"] =True
    my_thread_apagarsensor=None
    my_thread_apagarsensor = threading.Thread(target=apagarsensor)
    my_thread_apagarsensor.start()









def reinicio_variables():
    global plantas_iluminadas,peces_alimentados,plantas_humectadas, agua_circulada,agua_oxigenada,agua_aireada
    plantas_iluminadas = False
    peces_alimentados = False
    plantas_humectadas = False
    agua_circulada = False
    agua_oxigenada = False
    agua_aireada = False



def Update_Actuator():
    global Val_Actuadores
    #os.system('mosquitto_pub -h localhost -t "main/actuators" -m "'+json.dumps(Val_Actuadores)+'"')
    


#loop
cambio_ciclo=True
ciclo=ciclo_dia()
ciclo_anterior=ciclo-1
actuadores_act='0'
actuadores_ant='1'
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

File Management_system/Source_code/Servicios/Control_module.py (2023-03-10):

import json

porc_iluminacion = 0.8  #Debe ser float entre 0 y 1
porc_humectacion = 0.0  #Debe ser float entre 0 y 1, se asume el mismo para ambos niveles
porc_circulacion = 0.99  #Debe ser float entre 0 y 1
porc_oxigenacion = 0.99
porc_aireacion = 0.2





x = {
"porc_iluminacion": 0.8,
"porc_humectacion": 0.4,
"porc_circulacion": 0.99,
"porc_oxigenacion": 0.99,
"porc_aireacion":  0.2,
}

# convert into JSON:
y = json.dumps(x)


def Porcentajes(ciclo):
    global x

    #00:00-02:00
    if ciclo ==  1:
        x = {"porc_iluminacion": 0,"porc_humectacion": 0,"porc_circulacion": 0.99,"porc_oxigenacion": 0.99,"porc_aireacion":  0}
    #02:00-04:00
    elif ciclo ==  2:
        x = {"porc_iluminacion": 0,"porc_humectacion": 0,"porc_circulacion": 0.99,"porc_oxigenacion": 0.99,"porc_aireacion":  0}
    #04:00-06:00
    elif ciclo ==  3:
        x = {"porc_iluminacion": 0,"porc_humectacion": 0,"porc_circulacion": 0.99,"porc_oxigenacion": 0.99,"porc_aireacion":  0}
    #06:00-08:00
    elif ciclo ==  4:
        x = {"porc_iluminacion": 0.99,"porc_humectacion": 0,"porc_circulacion": 0.99,"porc_oxigenacion": 0.99,"porc_aireacion":  0}
    #08:00-10:00
    elif ciclo ==  5:
        x = {"porc_iluminacion": 0.99,"porc_humectacion": 0,"porc_circulacion": 0.99,"porc_oxigenacion": 0.99,"porc_aireacion":  0.99}
    #10:00-12:00
    elif ciclo ==  6:
        x = {"porc_iluminacion": 0.99,"porc_humectacion": 0,"porc_circulacion": 0.99,"porc_oxigenacion": 0.99,"porc_aireacion":  0.99}
    #12:00-14:00
    elif ciclo ==  7:
        x = {"porc_iluminacion": 0.99,"porc_humectacion": 0,"porc_circulacion": 0.99,"porc_oxigenacion": 0.99,"porc_aireacion":  0.99}
    #14:00-16:00
    elif ciclo ==  8:
        x = {"porc_iluminacion": 0.99,"porc_humectacion": 0,"porc_circulacion": 0.99,"porc_oxigenacion": 0.99,"porc_aireacion":  0.99}
    #16:00-18:00
    elif ciclo ==  9:
        x = {"porc_iluminacion": 0.99,"porc_humectacion": 0,"porc_circulacion": 0.99,"porc_oxigenacion": 0.99,"porc_aireacion":  0.99}
    #18:00-20:00
    elif ciclo ==  10:
        x = {"porc_iluminacion": 0.99,"porc_humectacion": 0,"porc_circulacion": 0.99,"porc_oxigenacion": 0.99,"porc_aireacion":  0.99}
    #20:00-22:00
    elif ciclo ==  11:
        x = {"porc_iluminacion": 0.99,"porc_humectacion": 0,"porc_circulacion": 0.99,"porc_oxigenacion": 0.99,"porc_aireacion":  0}
    #22:00-24:00
    elif ciclo ==  12:
        x = {"porc_iluminacion": 0,"porc_humectacion": 0,"porc_circulacion": 0.99,"porc_oxigenacion": 0.99,"porc_aireacion":  0}
    return x

import subprocess as sp

def get_Porcentajes_predictivo():
    #set_point_temp=22
    #ciclos=get_ciclos_control(22)
    x = sp.getoutput("cat /home/acuaponito/Desktop/Servicios/Ram_Var/ciclos_pred.txt")
    return json.loads(x)

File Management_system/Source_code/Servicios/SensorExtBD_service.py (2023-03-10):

#!/usr/bin/python3
import paho.mqtt.client as mqtt  #import the client1
import time
import json
import datetime as dt
import pyrebase
import subprocess as sp
config = json.loads(sp.getoutput('cat firebase-credentials.json'))

firebase = pyrebase.initialize_app(config)
database = firebase.database()




def on_connect(client, userdata, flags, rc):
    if rc==0:
        client.connected_flag=True #set flag
        print("connected OKa")
    else:
        print("Bad connection Returned code=",rc)
errores=0        
def on_message(client, userdata, message,tmp=None):
    global errores
    print("mensajito")


def sentBD(result):
    database.child("DatosSensoresExterno").push(result)


def on_message_Ligth(client, userdata, message,tmp=None):
    global errores
    try:
        result={"fecha":dt.datetime.now().strftime("%m/%d/%Y, %H:%M:%S"),
            "tipo": "Ligth",
            "valor": str(message.payload,'utf-8')}
        sentBD(result)
    except:
        errores=1
def on_message_HumTemp(client, userdata, message,tmp=None):
    global errores
    try:
        print("falta por definir")
        #sentBD("TempHum",message)
    except:
        errores=1








mqtt.Client.connected_flag=False#create flag in class
broker='localhost'
client = mqtt.Client("SensoresExtBD")             #create new instance 
client.on_connect=on_connect  #bind call back function
client.on_message = on_message


client.message_callback_add('Main/sensorExr/Ligth', on_message_Ligth)
client.message_callback_add('Main/sensorExr/HumTemp', on_message_HumTemp)






client.loop_start()
print("Connecting to broker ",broker,1883)
client.connect(broker,1883)      #connect to broker
while not client.connected_flag: #wait in loop
    print("In wait loop")
    time.sleep(1)
print("in Main Loop")
client.subscribe("Main/sensorExr/#")
while not errores:
    time.sleep(1)
    continue
#client.loop_forever()

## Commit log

2023-01-22 comiit de luis
2023-01-22 el commit mio
2023-02-15 estructura de carpetas
2023-02-15 add new things
    [pieza1.STL, pieza2.STL, pieza3.STL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]
2023-03-10 litle changes
    [pieza1.STL, pieza2.STL, pieza3.STL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]
2023-03-11 adition doc
    [ControlValidation.xlsx]
2023-03-11 changes control
    [PruebaCorrelacion (1).xlsx, data_set2_completoControlModerno.xlsx, data_set_moderno_final (1).xlsx]
2023-03-12 adition of fuzzy
    [Estimulos.xlsx]
2023-03-13 change ubi
    [Estimulos.xlsx]
